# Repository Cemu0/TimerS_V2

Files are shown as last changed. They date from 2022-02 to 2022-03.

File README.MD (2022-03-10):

# TIMERS V2 by Cemu0

## I'm lazy to read, give me some video :) 

Watch the video (https://youtu.be/iN_e02LLBGo)

<!-- <iframe width="560" height="315" src="https://www.youtube.com/embed/iN_e02LLBGo" title="YouTube video player" frameborder="0" allow="accelerometer; autoplay; clipboard-write; encrypted-media; gyroscope; picture-in-picture" allowfullscreen></iframe> -->

## WHAT IS THIS?

- [x] And you also need to control your gardens watering, pumps or lights **by schedule**?
  
- [x] You don't wanna buy **multiple timers** and want a centralised control hub?

- [x] You need timerS with **Global** connection & **control** but you also need it to **work offline**?

## HOW YOU SOLVE THAT?

- By using ESPHome you can create your timers without knowing much about C++ code (except you want to modify this repo).

- This will connect to your Home Assistant(HA) via an MQTT broker to provide remote control. I personally found that tracking the history of each relay through HA is quite useful for debugging and tracking the watering status of plans.

- This will use an SD card to save your schedules and will turn on/off your devices according to that schedule, therefore you don't need an internet or wifi connection to run your stuff schedule.

## LIMITATION 

- This repo doesn't have any TIME menu, so you need to have a wifi connection to set the time automatically over SNTP.

- Currently, this repo code only supports 8 relays, but in theory, you can extend it to ... IDK, 10 relays without external module and 8x8x5 = 320? relays (in theory) with pcf8574_hubs. Moreover in theory this can control others in LAN devices with a bit change in [code]https://github.com/esphome/feature-requests/issues/52). But I leave that to you.

- The number of schedule control for each relay is not limited (it should work well up to a hundred timers in total).

Note: Although all the relays will be connected to HA without any config and you can control any Relay directly, the online control just replaces the screen with text sensors (with you should disable history track in HA of this) and a cover (like the gate control ) so it is quite hard to control online.
 
## INSTRUCTION 
### REQUIREMENT:
#### Hardware:
- Wemos D1 R32 board.
- A logging shield for Arduino (you can use an SD card module and an RTC module like ds1307, but you will need to wring a lot, so I found that modifying the shield make things a lot easier), Also prepare an SD card too (should be lower than 
Rotary encoder module to navigate through the menu. If you only want to control through the internet, you can skip this, but it will be quite hard to control.
- 20x4 LCD screen come with an I2C module.
- Relay module, any relay module with low-level control (if 5v) should work you can use an SSR relay module like mine, since the SSR does not create sparks when triggered this can provide more stability for the esp, but in fact, I used the traditional relay module with esp32 for years without any problems until now (even without any snubber). To be safe if you using a contact relay module you should add a snubber circuit through each load to prevent EMI from killing your circuit. 
- You can choose to add a DTH sensor for ... fun, I mean to measure the temp and hump. Thanks to espHome this value also report to your HA.
- Some things to put all that stuff into, A 3d print box design also comes with this repo.
#### Software:
- If you need the timer to work online or remote control, An MQTT broker is needed, I recommend using the [Home Assistant Add-on: Mosquitto broker](https://github.com/home-assistant/addons/blob/master/mosquitto/DOCS.md) for easy setup 
- To upload the code you need to [install ESPHome on your local machine by using python](https://esphome.io/guides/installing_esphome.html), but in fact, you can simply plug the device into your HA server to flash the ESP through the [ESPHome extension](https://esphome.io/guides/getting_started_hassio.html), anyway in my case this system run remotely so I use my local machine to upload the code. 

### STEP 1: Wiring

If you were familiar with ESPhome, you can simply check out the config file (timer.yaml) to see with connections go.  
If using a logging shield you can skip the SPI and I2C connection wiring for the RTC. But you should cut the back of the shield-like this if you plan to use pins 36 & 39 because this board was designed for Arduino and those pins only accept input.
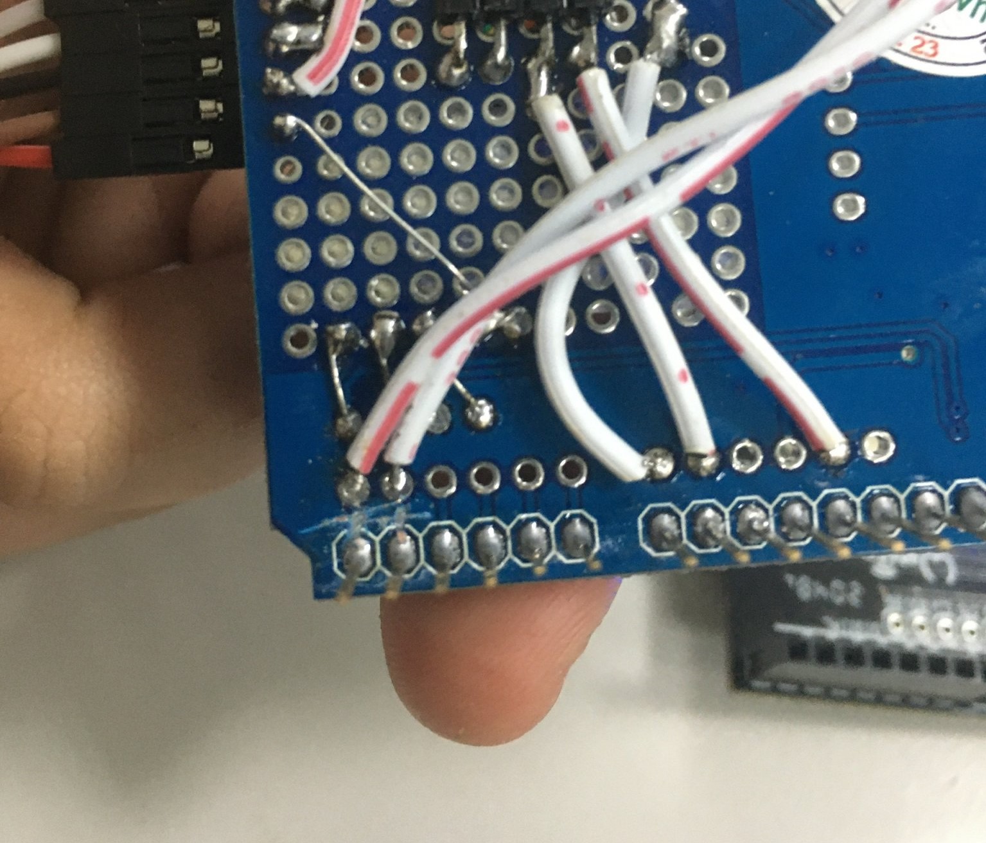
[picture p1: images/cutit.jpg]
cutpin

We will use the default SPI connection, so it going like this.  
> **SD_CS 5**  
**SCK_PIN 18**  
**MISO_PIN 19**  
**MOSI_PIN 23**  

And the RTC module, the LCD screen needs to connect to this bus too (the 21 & 22 pins already labelled as SDA & SCL in R32 board). Note that if you use the pcf8574, you should use other I2C pins because in my case using this can lead to many bugs, like RTC and LCD not working and I am not sure why)  
> **SDA 21**  
**SCL 22**  

The encoder module will be like, you can swap DT and CLK pins or pin numbers in setup to revert scroll direction.  
> **SW 16**  
**DT 14**  
**CLK 27**  

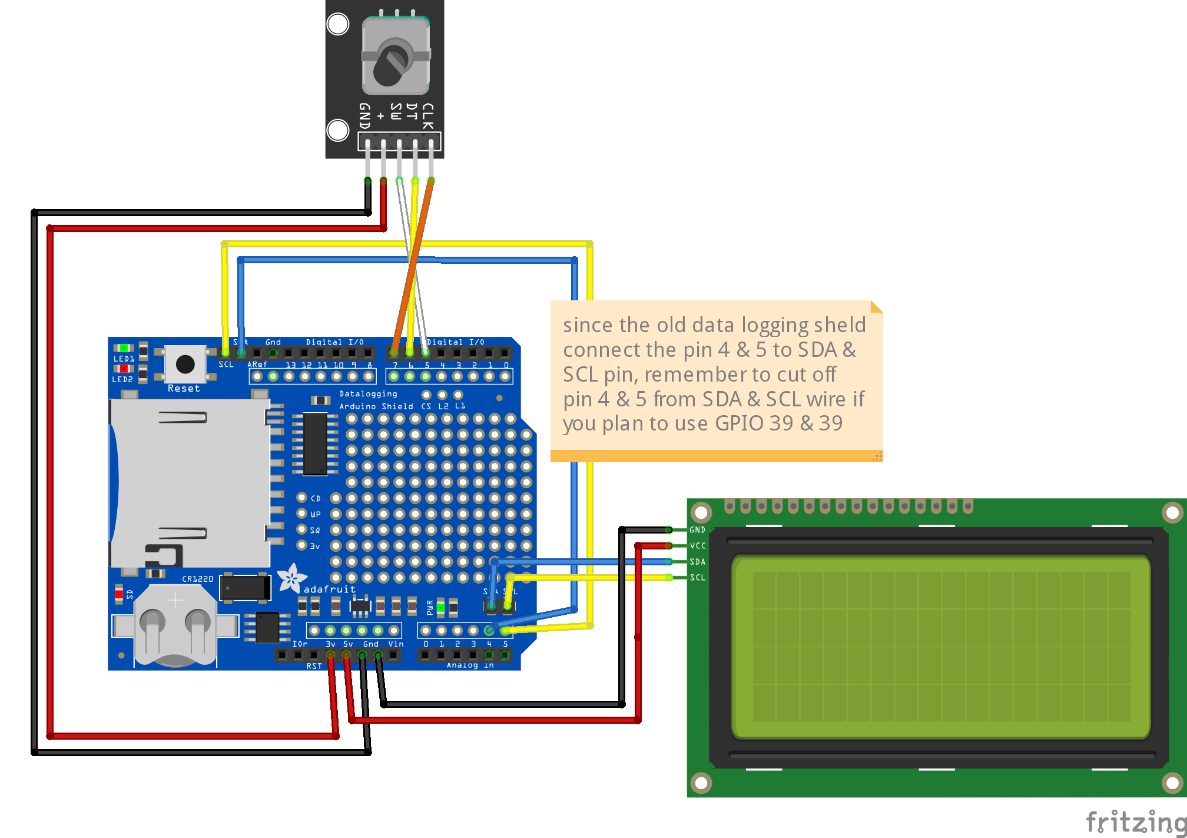
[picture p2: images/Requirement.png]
requirement


**Important NOTE:** [you need to add a 330ohm resistor to keep the Wifi connection on the R32 board stable](https://github.com/espressif/arduino-esp32/issues/2144#issuecomment-657672609)

After doing that connection, you basically complete the necessary wire, now the relay timer need relays. You can use my pins config below
> **relay1: 2**  
**relay2: 4**  
**relay3: 12**  
**relay4: 13**  
**relay5: 33**  
**relay6: 25**  
**relay7: 26**  
**relay8: 32**  

*NOTE:* if you use the pcf8574 board you can use any relay pin above to set up an I2C connection. Importantly, I tested the pcf8574 with the relays, everything worked without load, but if have a load on the AC side, the pcf8574 reset itself and lost control for a while. I'm not clearly sure why. This held event using SSR relay (SSR do reduce the problem), and it looks like many people get [the same issue](https://www.letscontrolit.com/forum/viewtopic.php?t=7043) at this so can try another pin expand boards, add snubber or move the expansion board faraway from relays module.

If you want to connect to a sensor, you can use pin 15 or 17 for this reason. 
> **DTH data pin: 15**

Full connection going like this
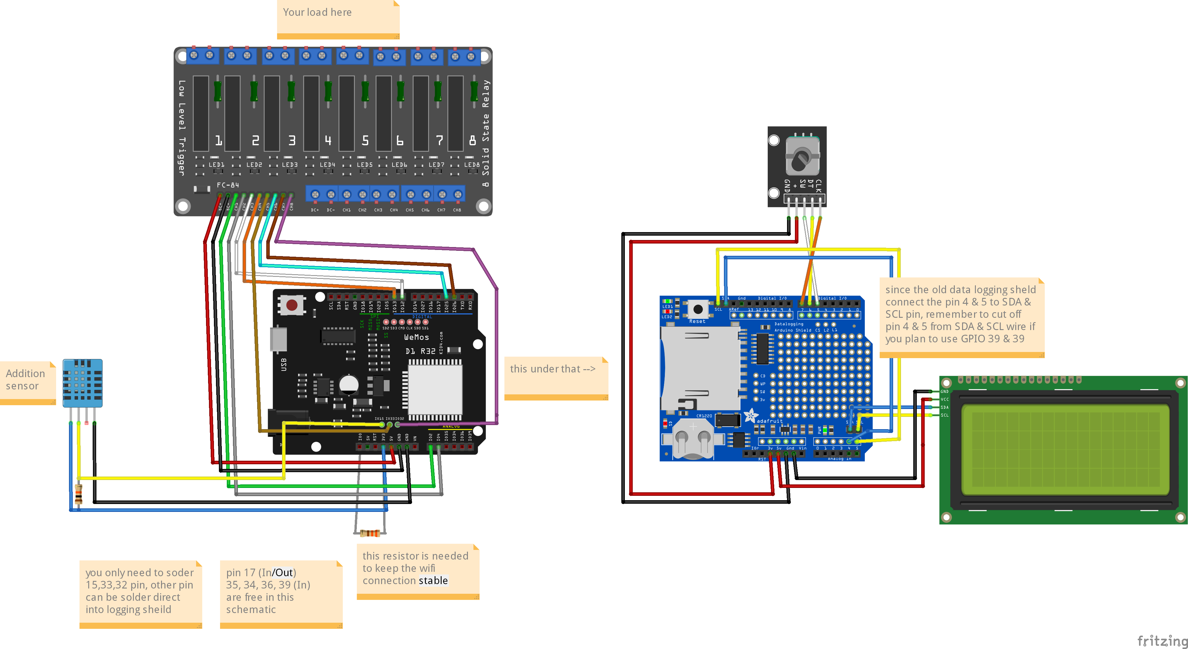
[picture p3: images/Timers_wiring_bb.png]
fully connection


### STEP2: Upload
Download this repo and open it in your favourite editor (like the VScode) 

Edit the "timer.yaml" file (wifi, MQTT, OTA setting or pins) to your custom setup.
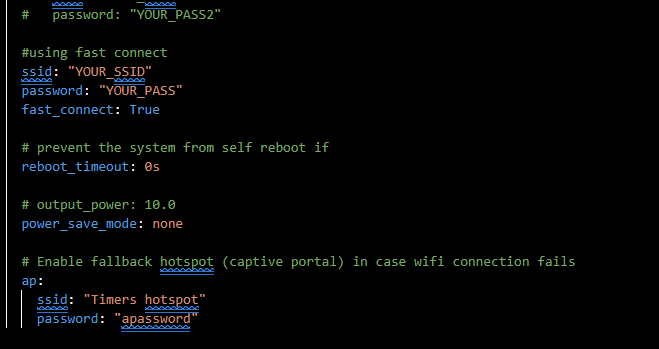
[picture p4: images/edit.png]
edit


Plugging in your hardware (the MicroUSB on esp32 board) and upload the code by running `esphome timers.yaml upload` inside the repo directory

### STEP3: Enjoy
After upload, if your wiring correctly, you should be able to use the project. Again the first time you boot the system, you will need to have a WiFi connection to let the ESP set the RTC time automatically. After that, you needn't.
If you don't know about [ESPhome](https://esphome.io/index.html), go and check out many devices you can integrate with.

[0]: images/cutit.jpg
[1]: images/Requirement.png
[2]: images/Timers_wiring_bb.png
[3]: images/edit.png

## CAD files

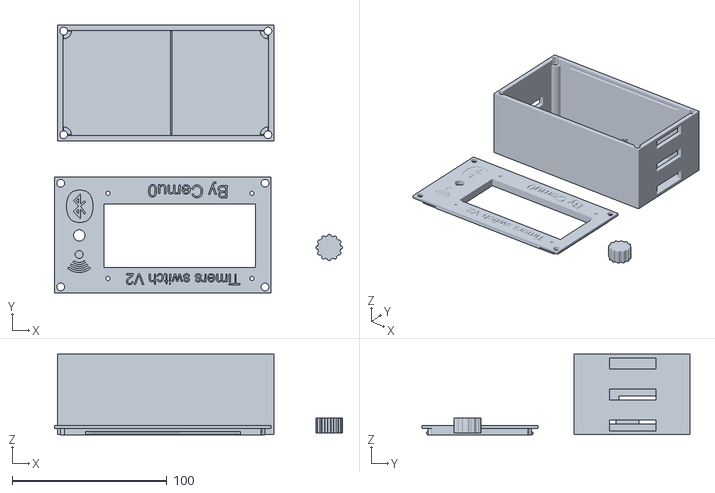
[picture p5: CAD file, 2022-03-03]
box/TimerV2 v8.stl
186.1 x 173.3 x 52.0

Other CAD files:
box/TimerV2_box_design.f3d

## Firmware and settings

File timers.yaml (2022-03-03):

esphome:
  name: cemu0timers
  platform: ESP32
  board: wemos_d1_mini32
  includes:
    - timer_manager.h
    - screens.h
    - UI.h

  on_boot:
  - then:
      # read the RTC time once when the system boots
      ds1307.read_time:

  #turn on screen when boot ? 
  - priority: 100
    then:
      - switch.turn_on: screenlight

wifi:
  id: swifi

  #using normal connect
  # networks:
  # - ssid: "YOUR_SSID1"
  #   password: "YOUR_PASS1"
  # - ssid: "YOUR_SSID2"
  #   password: "YOUR_PASS2"

  #using fast connect
  ssid: "YOUR_SSID"
  password: "YOUR_PASS"
  fast_connect: True

  # prevent the system from self reboot if 
  reboot_timeout: 0s

  # output_power: 10.0
  power_save_mode: none

  # Enable fallback hotspot (captive portal) in case wifi connection fails
  ap:
    ssid: "Timers hotspot"
    password: "apassword"

#fallback mechanism, can be disabled if you sure your wifi connection config is corrected 
captive_portal:

# Enable logging
logger:

# disable Home Assistant API by default to use MQTT !

mqtt:
  id: smqtt
  broker: your.mqtt.broker.duckdns.net
  #note that currently ESPHome not yet support MQTT secure so you should have to use port 1883 as an unsecure port https://github.com/esphome/feature-requests/issues/133
  port: 1883
  username: your_mqtt_username
  password: your_mqtt_password

i2c:
  - id: bus_a
    sda: 21
    scl: 22
    scan: false
    frequency: 200kHz

  #incase you use an external control like a pcf8574_hub and not use direct GPIO
  # - id: bus_b
  #   sda: 25
  #   scl: 26
  #   scan: false
  #   frequency: 10kHz

ota:
   safe_mode: false
   password: "your_ota_pass"

# Example configuration entry if use pcf8574
# pcf8574:
#   - id: 'pcf8574_hub'
#     i2c_id: bus_b
#     address: 0x20 
#     pcf8575: false

globals:
   - id: screen_on
     type: bool
     restore_value: no
     initial_value: '1'

  #  - id: screen_page
  #    type: int
  #    restore_value: no
  #    initial_value: '1'


time:
    #   0x68
  - platform: ds1307
    # repeated synchronization is not necessary unless the external RTC
    # is much more accurate than the internal clock
    update_interval: never
    i2c_id: bus_a

  - platform: sntp
    id: my_time
    on_time_sync:
      then:
        # ... and update the RTC when the synchronization was successful
        ds1307.write_time:

switch:
  # - platform: gpio
  #   id: relay8
  #   pin: 2
  #   name: "Test LED"
    
  - platform: template
    name: "Screen Led Control"
    id: screenlight
    internal: True
    optimistic: True
    turn_on_action:
      then:
        - delay: 5min
        - switch.turn_off: screenlight

  - platform: gpio
    name: "Relay 1"
    id: relay0
    restore_mode: ALWAYS_OFF
    pin:
      # pcf8574: pcf8574_hub
      # Use pin number 0 in case pcf8574_hub and go on with other relay !
      number: 2
      # One of INPUT or OUTPUT
      mode: OUTPUT
      inverted: false

  - platform: gpio
    name: "Relay 2"
    id: relay1
    restore_mode: ALWAYS_OFF
    pin:
      # pcf8574: pcf8574_hub
      number: 4
      mode: OUTPUT
      inverted: false

  - platform: gpio
    name: "Relay 3"
    id: relay2
    restore_mode: ALWAYS_OFF
    pin:
      # pcf8574: pcf8574_hub
      number: 12
      mode: OUTPUT
      inverted: false
      
  - platform: gpio
    name: "Relay 4"
    id: relay3
    restore_mode: ALWAYS_OFF
    pin:
      # pcf8574: pcf8574_hub
      number: 13
      mode: OUTPUT
      inverted: false

  - platform: gpio
    name: "Relay 5"
    id: relay4
    restore_mode: ALWAYS_OFF
    pin:
      # pcf8574: pcf8574_hub
      # number: 17 #this pin has been burn off by me 
      number: 33
      mode: OUTPUT
      inverted: false

  - platform: gpio
    name: "Relay 6"
    id: relay5
    restore_mode: ALWAYS_OFF
    pin:
      # pcf8574: pcf8574_hub
      number: 25
      mode: OUTPUT
      inverted: false
      
  - platform: gpio
    name: "Relay 7"
    id: relay6
    restore_mode: ALWAYS_OFF
    pin:
      # pcf8574: pcf8574_hub
      number: 26
      mode: OUTPUT
      inverted: false

  - platform: gpio
    name: "Relay 8"
    id: relay7
    restore_mode: ALWAYS_OFF
    pin:
      # pcf8574: pcf8574_hub
      number: 32
      mode: OUTPUT
      inverted: false

  - platform: restart
    name: "Timers Restart"

sensor:
  - platform: rotary_encoder
    id: encoder
    name: "Rotary Encoder"
    resolution: 2
    pin_a: 14
    pin_b: 27
    internal: True
    # last_reset_type: ""
    on_clockwise:
      - switch.turn_on: screenlight
      # - component.update: my_display
    on_anticlockwise:
      - switch.turn_on: screenlight
      # - component.update: my_display

  - platform: wifi_signal
    id: wfsig
    name: "WiFi Signal Sensor"
    update_interval: 600s

  - platform: dht
    pin: 15
    model: DHT11
    temperature:
      name: "Garden Temperature"
      id: dthsensor1tmp
    humidity:
      name: "Garden Humidity"
      id: dthsensor1hmd
    update_interval: 60s
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

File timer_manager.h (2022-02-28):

#pragma once
#include "esphome.h"

#include <vector>
using namespace std;

#define USER_COUNT 1
#define UPDATE_TIMER_TIME 1000

#define MAX_RELAY 8

template <class I>
String FormatDigit(I data){
    if(String(data).length()<2)return "0" + String(data);
    return String(data);
}

enum timerStuff{
    START_HOUR = 0,
    START_MINUTE = 1,
    END_HOUR = 2,
    END_MINUTE = 3,
};

struct relay_time{
    // h_start,m_start,h_end,m_end
    byte time[4] = {0,0,0,0};
    //since bit field not suitable i just use a byte here
    // nope sat fri thu wed tue mon sun
    byte date = 0b01111111;
    
    // Mon to Sun : 0 to 6
    bool activateDay(uint8_t day){
        return (date & (1<<day));
    }
};

vector<vector<relay_time>> timer_vector;

#define TARGET_RELAYS {id(relay0),id(relay1),id(relay2),id(relay3),id(relay4),id(relay5),id(relay6),id(relay7)} //,id(relay8)
        

//timer menu
class timer_manager : public Component{ //
private:
    unsigned long long update_time;
    
public:
    bool activate = true;

    void toggleRelayState(int relay){
        //need to reload every time 
        gpio::GPIOSwitch taget_relay[] = TARGET_RELAYS;
        //NOTE: taget_relay[relay].toggle(); //not work :(
        changeRelayState(relay,!taget_relay[relay].state);
    }
    void changeRelayState(int relay, bool state){
        gpio::GPIOSwitch taget_relay[] = TARGET_RELAYS;
        if(taget_relay[relay].state == state)
            return;
        //TODO: looking for a better way 
        switch (relay)
        {
        case 0:
            id(relay0).toggle();
            break;

        case 1:
            id(relay1).toggle();
            break;

        case 2:
            id(relay2).toggle();
            break;

        case 3:
            id(relay3).toggle();
            break;
        
        case 4:
            id(relay4).toggle();
            break;
        
        case 5:
            id(relay5).toggle();
            break;
        
        case 6:
            id(relay6).toggle();
            break;
        
        case 7:
            id(relay7).toggle();
            break;

        default:
            break;
        }
    }

    // void changeRelayState(int relay, bool state){
    //     gpio::GPIOSwitch taget_relay[] = TARGET_RELAYS;
    //     if(taget_relay[relay].state)
    //     {
    //         if(!state)
    //             taget_relay[relay].turn_off();
    //             // taget_relay[relay].publish_state(false);
    //     }
    //     else
    //     {
    //         if(state)
    //             taget_relay[relay].turn_on();
    //             // taget_relay[relay].publish_state(true);
    //     }     
    // }
    //work
    bool checkRelayStage(int relay){
        gpio::GPIOSwitch taget_relay[] = TARGET_RELAYS;
        return taget_relay[relay].state;
    }

    relay_time* addTimer(int relay){
        relay_time rt;
            rt.date = 0b01111111;
            rt.time[0] = 0;
            rt.time[1] = 0;
            rt.time[2] = 0;
            rt.time[3] = 0;
        timer_vector[relay].push_back(rt);

        return &timer_vector[relay].back();
    }

    bool removeTimer(int relay, int timerNo){
        if(timer_vector[relay].size() <= timerNo)
            return false;
        timer_vector[relay].erase(timer_vector[relay].begin() + timerNo);
        return true;
    }

    relay_time* getTimer(int relay, int timerNo){
        if(timer_vector[relay].size() <= timerNo)
            ESP_LOGE("relay_time", "access out of range !!!");
        return &timer_vector[relay][timerNo];
    }

    int numOftimer(int relay){
        return timer_vector[relay].size();
    }


	// 0	1		0	0	:	0	0		0	0	:	0	0		A	L	L	
	// 0	2		0	0	:	0	0		0	0	:	0	0		N	O		
	// 0	3		0	0	:	0	0		0	0	:	0	0		C	U	S	M

    String print_Time(int relay, int timerNo){
        if(timer_vector[relay].size() <= timerNo)
            return "none";
        relay_time timer = timer_vector[relay][timerNo];
        String data = " " + FormatDigit(timerNo + USER_COUNT) + " " + FormatDigit(timer.time[0]) + ":" + 
                            FormatDigit(timer.time[1]) + " " + 
                            FormatDigit(timer.time[2]) + ":" + 
                            FormatDigit(timer.time[3]) + " ";
        //old with not usefull 
        // for(int i = 0; i<7;i++){
            // data+=(timer.date & (1<<i))?"y":"n";
        // }

        if(timer.date == 0){
            data+="NO ";
        }else if(timer.date == 0b01111111){ // 7 bit high 
            data+="ALL";
        }else {
            data+="CUS";
        }

        return data;
    }

    void setup() override {

    }
    
    void loop() override {
        if(activate)
            if((unsigned long long) update_time - millis() > UPDATE_TIMER_TIME){
                update_time = millis();


                for(int relay = 0; relay < MAX_RELAY; relay++)
                    for (auto timer : timer_vector[relay])
                    {
                    auto now_time = my_time->now();
                    //hour
                    //minute
                    //day of the week; sunday=1 [1-7] mon 
                    if(timer.activateDay(now_time.day_of_week - 1)){
                        int state = -1; // do notthing
                        //should have a better way here but ... nope im too lazy for mathmatic and timing stuff
                        if(timer.time[START_HOUR] == now_time.hour &&  timer.time[START_MINUTE] == now_time.minute)
                            state = 1; // on
                        if(timer.time[END_HOUR] == now_time.hour &&  timer.time[END_MINUTE] == now_time.minute)
                            state = 0; // on
                        if(state != -1)
                            changeRelayState(relay,state);
                        };
                    }

            }
            // This will be called very often after setup time.
            // think of it as the loop() call in Arduino
    }

}timer_mng;

#include "FS.h"
#include "SD.h"
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
